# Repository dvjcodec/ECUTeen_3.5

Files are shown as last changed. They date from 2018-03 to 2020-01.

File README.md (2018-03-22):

# ECUTeen_3.5 rev.A (not tested!)

Stand Alone ECU with Teensy 3.5

On the board:
- 4 injection chanels
- 4 ignition chanels (for active coils)
- 2 high current PWM chanels
- IDLE out
- BOOST out
- stepper motor 
- 3x low current outs (FAN, FUEL, LC1)
- BlueTooth connector
- Clutch control
- tachometer out
- 5V power supply with LM2596
- 2x O2 sensor input
- CAN
- inlet air temperature sensor input
- coolant temperature sensor input
- throttle position sensor input
- 2x HALL input or VR
- MAP sensor 3bar

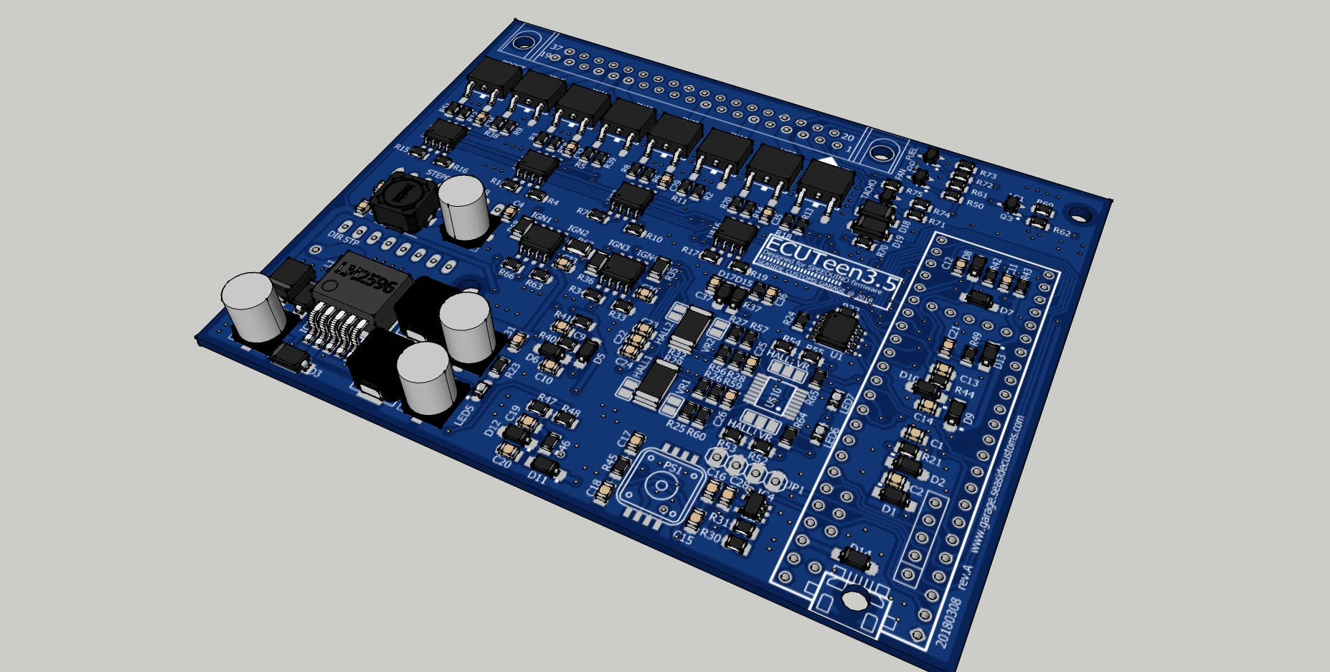
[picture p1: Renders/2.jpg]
Board


## Firmware

Designed for firmware
[Speeduino](https://speeduino.com/forum/viewtopic.php?f=13&t=1593)

## License

[CC BY-NC 3.0](https://creativecommons.org/licenses/by-nc/3.0/)

## Authors

Krzysztof Dymianiuk @ Seaside Customs Garage
http://www.garage.seasidecustoms.com

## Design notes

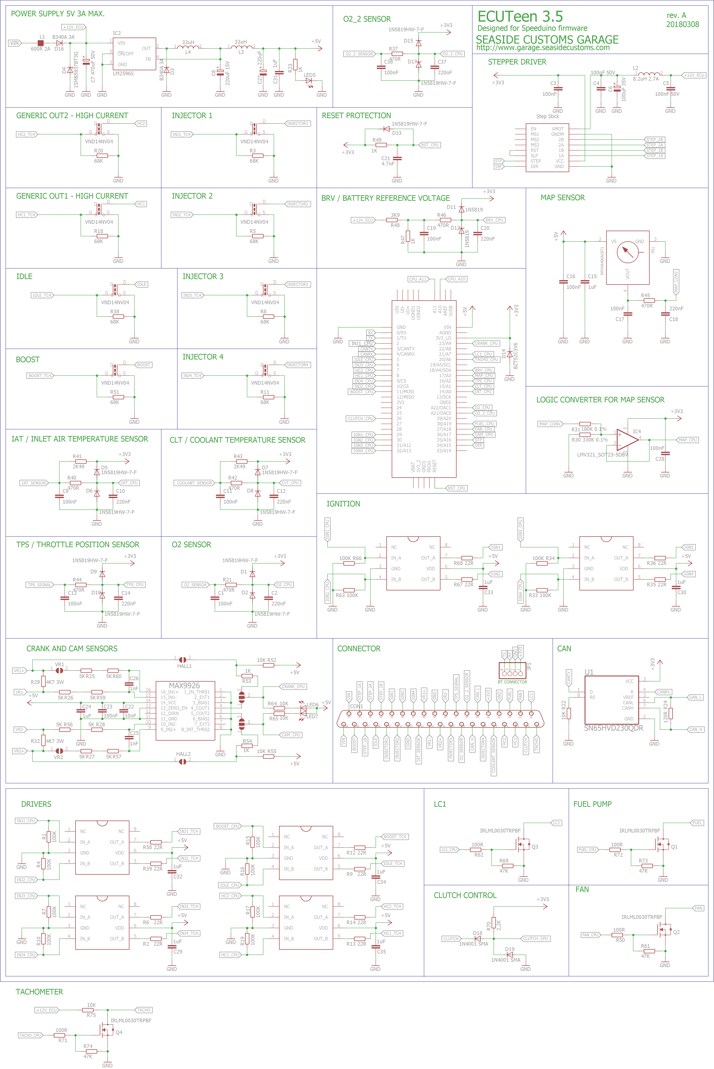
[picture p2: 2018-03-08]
schematic.png

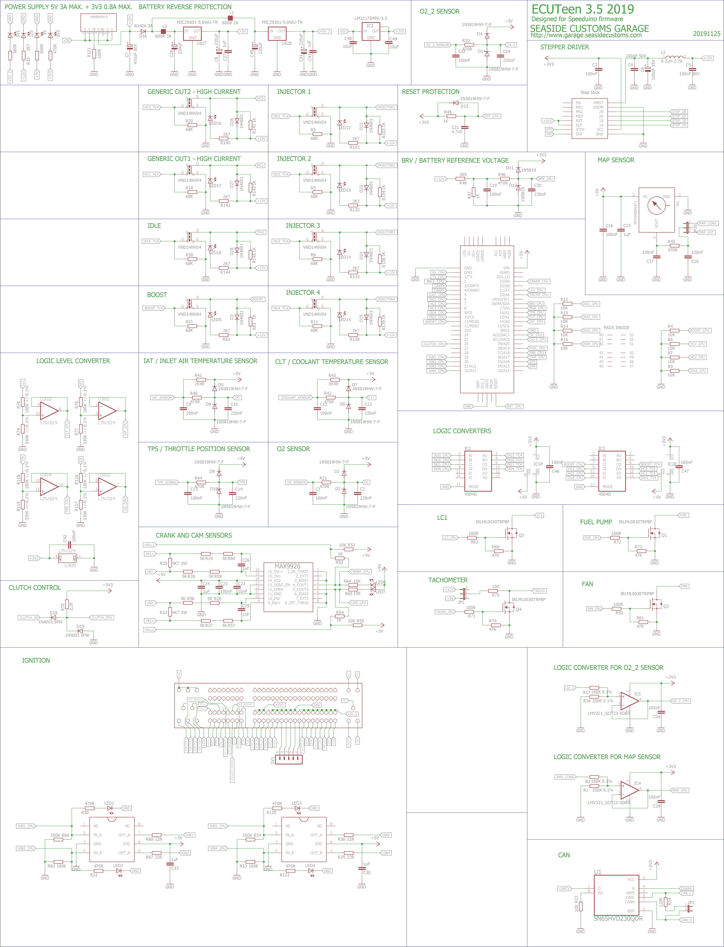
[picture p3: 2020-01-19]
ECUTeen3_5_2019_schematic.png

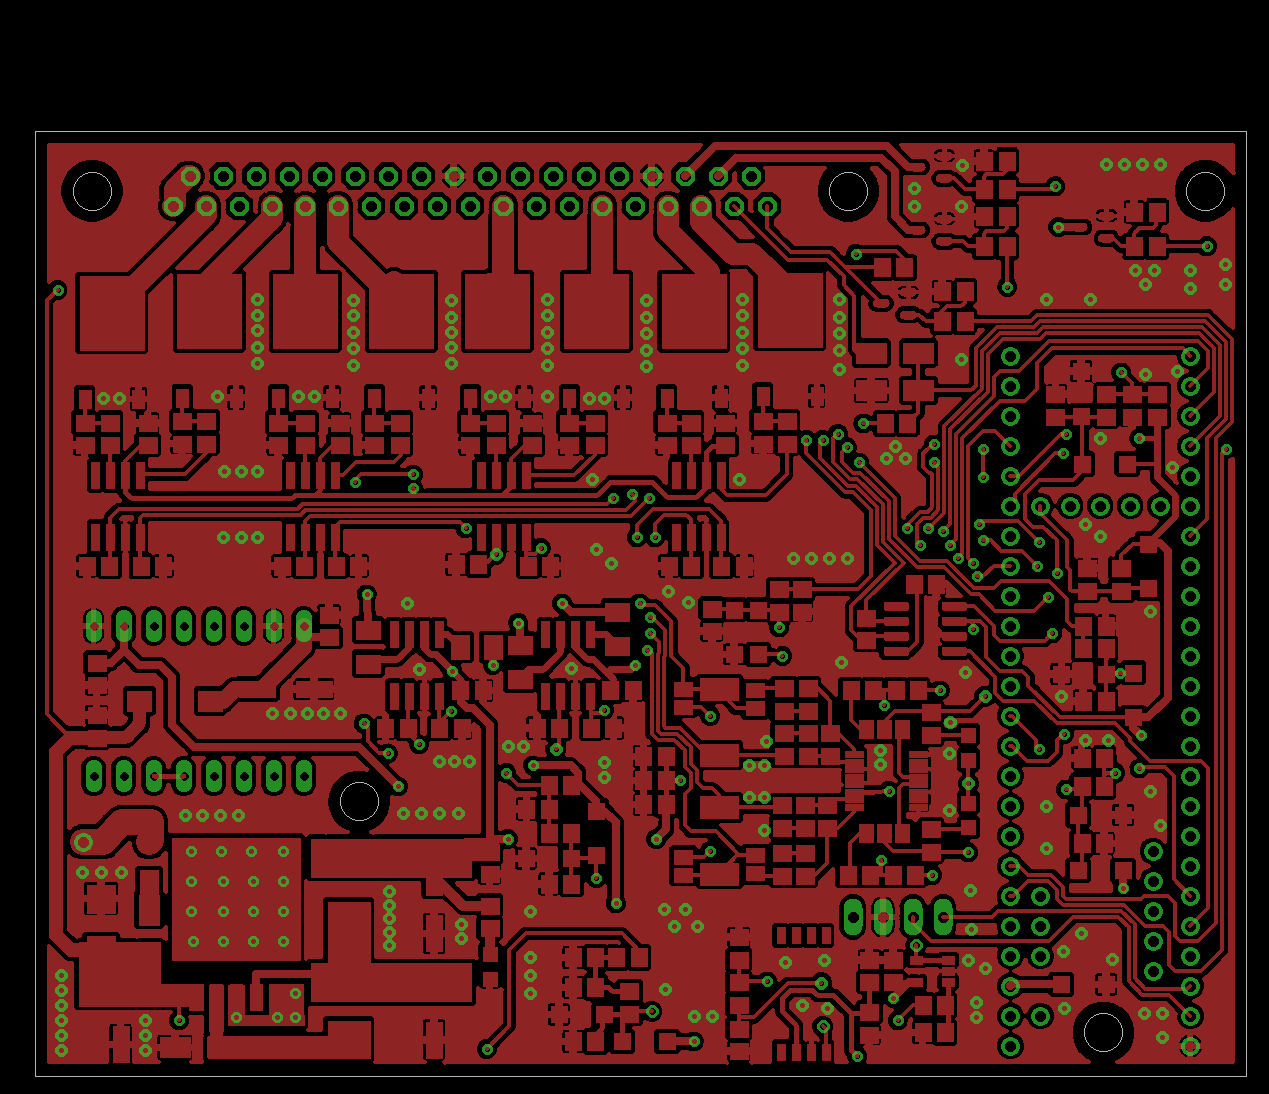
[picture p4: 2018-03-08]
Renders/TOP.png

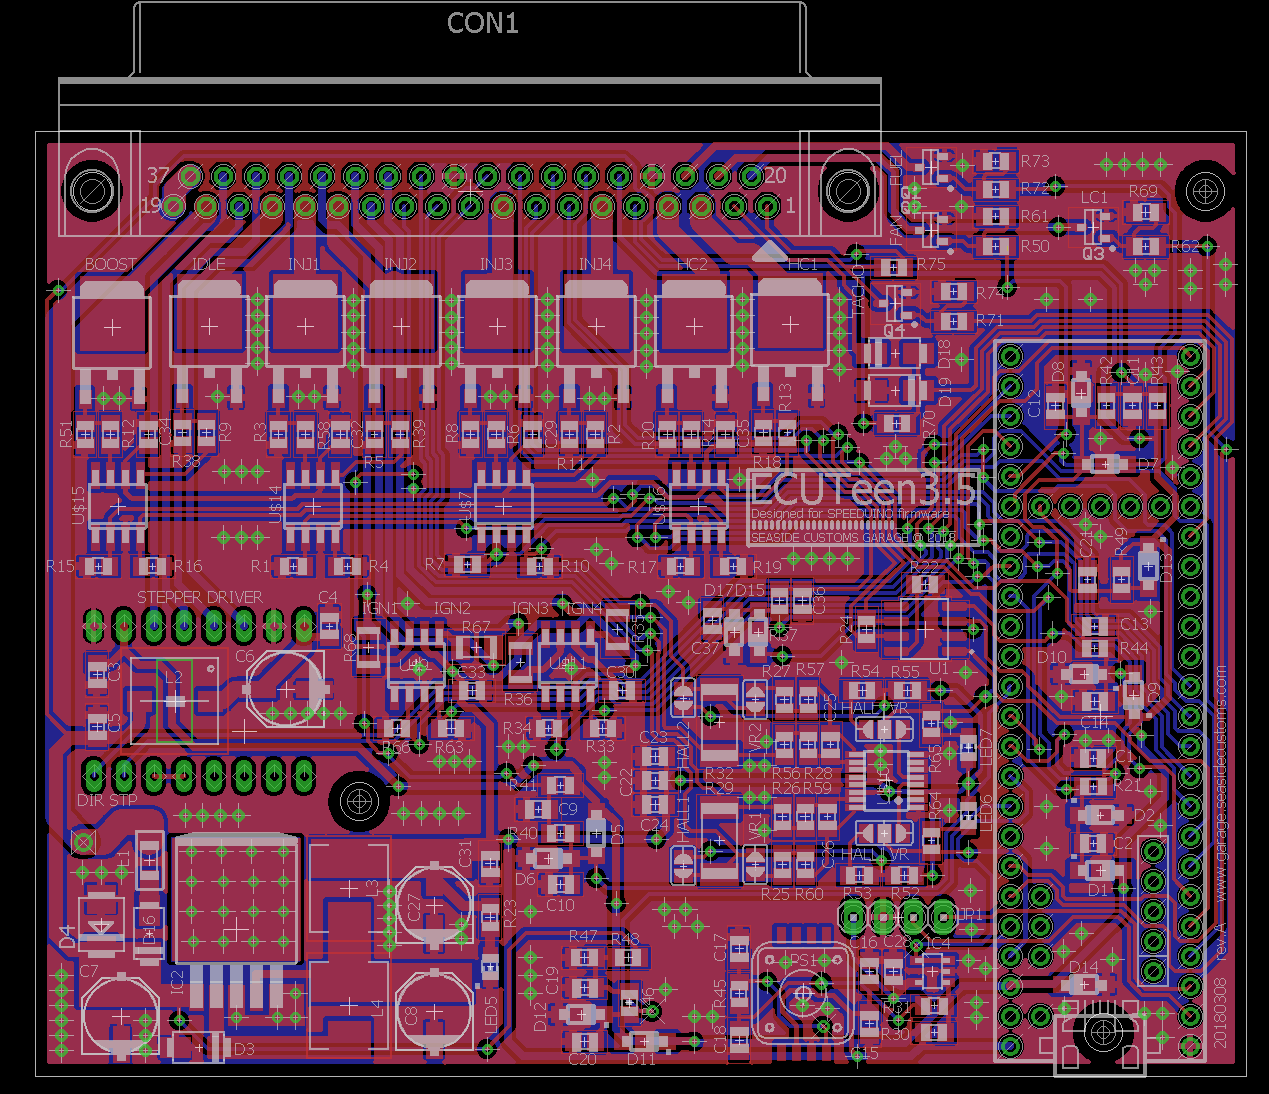
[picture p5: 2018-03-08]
Renders/ecuteen.png

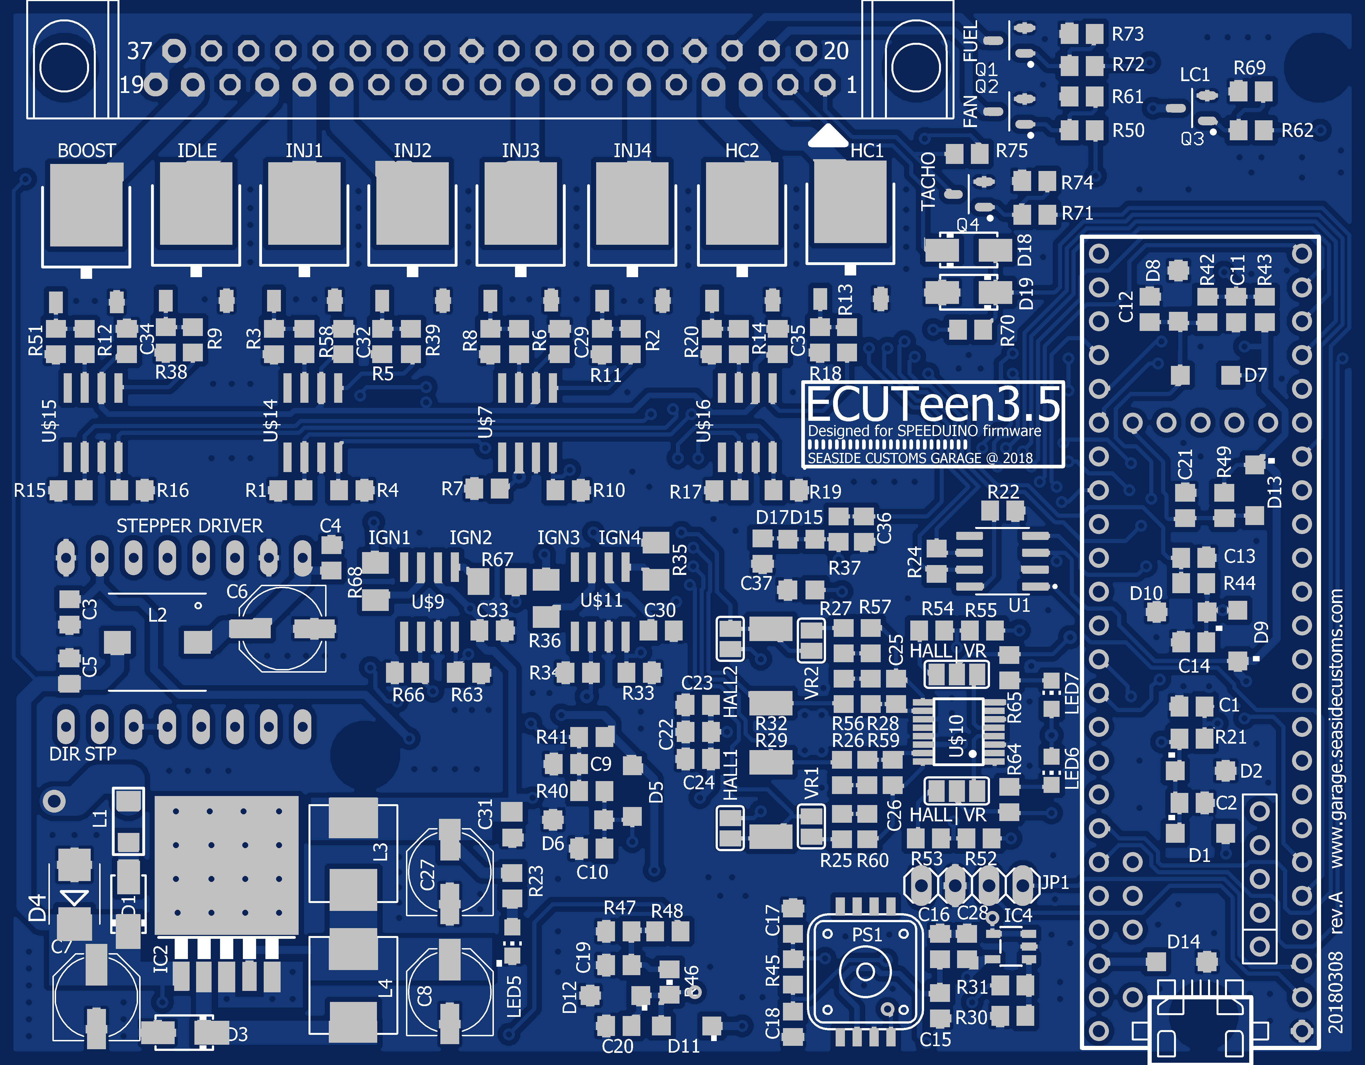
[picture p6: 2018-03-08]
Renders/eagleUp_ECUTeen3.5_rev.A_20180308_1928_board_top.png

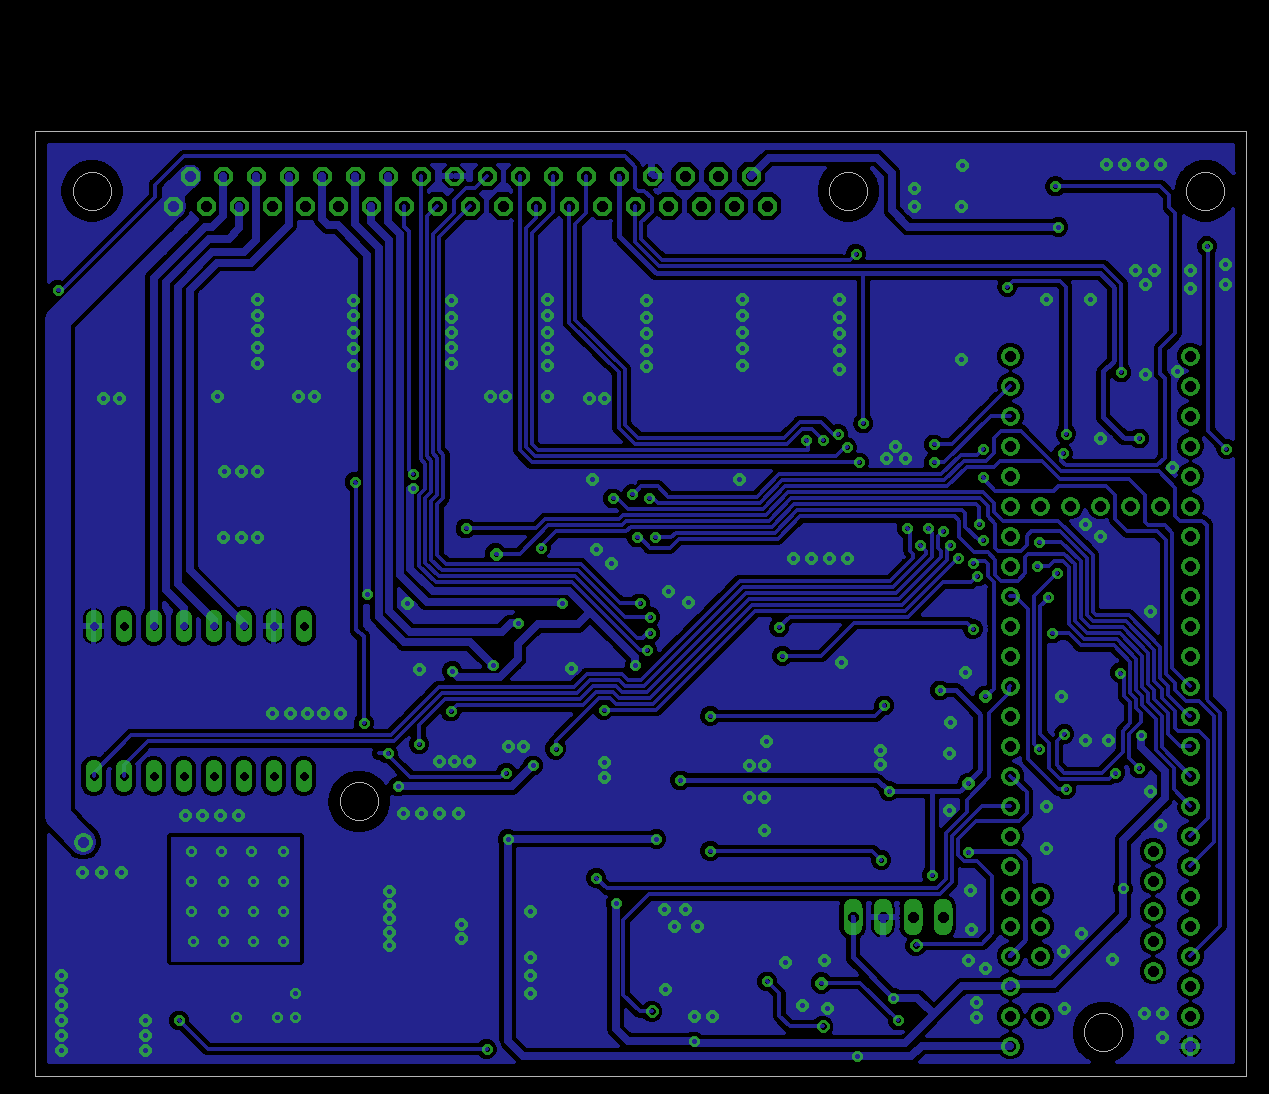
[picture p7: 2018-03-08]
Renders/BOTTOM.png

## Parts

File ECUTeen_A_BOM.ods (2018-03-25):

Element | Value | Package | Other | Link
C1, C3, C4, C5, C9, C11, C13, 16, C17, C19, C23, C28, C36, | 100nF | 0805 | C4,C5 – 50V, rest 35V
C2, C10, C12, C14, C18, C20, C37 | 220nF | 0805
C6 | 100uF/35V | CPOL, PANASONIC_D
C7 | 470uF/50V | CPOL, PANASONIC_D
C8, C27 | 220uF/35V | CPOL, PANASONIC_D
C15, C24, C29, C30, C31, C32, C33, C34, C35 | 1uF | 0805
C21 | 4.7nF | 0805
C22 | 10nF | 0805
C25, C26 | 1nF | 0805
CON1 | DB37 | male connector / angled
D1, D2, D5, D6, D7, D8, D9, D10, D13, D15, D17 | 1N5819HW-7-F | SOD123
D3, D16 | B340A 3A S1A | DO214AC
D4 | 1SMB5937BT3G | ZENER-DIODE SMB
D11, D12 | 1N5819 | SOD123
D14 | BZT52C3V6 | SOD123
D18, D19 | 1N4001 SMA S1A | DO214AC
IC2 | LM2596S | TO263-5 | Converter 150 kHz 3A Step-Down Voltage Regulator
IC4 | LMV321_SOT23-5DBV | SOT23-5
JP1 | PINHD-1X4 | Pin header 2.54
L1 | 600R 2A | L1206 | FERRITE BEAD Wurth 74279218
L2 | 8.2uH 2.7A | WE-PD_7332/7345_PLASTIC_BASE | WURTH 7447779008
L3, L4 | 33uH | WE-LHMI_7030/7050 | Wurth 74437349330
LED5, LED6, LED7 | LED DIODE | 0805
PS1 | MPXH6400AC6T1 | 1317A
Q1, Q2, Q3, Q4 | IRLML0030TRPBF | MOSFET-NCH_SOT-23
R1, R4, R7, R10, R15, R16, R17, R19, R33, R34, R63, R66 | 100K | 0805
R2, R6, R9, R12, R13, R14, R35, R36, R39, R58, R67, R68 | 22R | 0805
R3, R5, R8, R11, R18, R20, R38, R51 | 68K | 0805
R21, R37, R40, R42, R44, R45, R46 | 470R | 0805
R22, R52, R55, R64, R65, R75 | 10K | 0805
R23, R47, R49, R53, R54 | 1K | 0805
R24 | 120R | 0805
R25, R26, R27, R28, R56, R57, R59, R60 | 5K | 0805
R29, R32 | 4K7 3W | 2512
R30 | 330K 0.1% | 0805
R31 | 180K 0.1% | 0805
R41, R43 | 2K49 | 0805
R48 | 3K9 | 0805
R50, R62, R71, R72 | 100R | 0805
R61, R69, R73, R74 | 47K | 0805
R70 | 2K2 | 0805
U$1 | TEENSY_3.5
U$2, U$3, U$4, U$5, U$6, U$8, U$12, U$13 | VND14NV04 | DPAK
U$7, U$9, U$11, U$14, U$15, U$16 | TC427SO-8 | SO-8
U$10 | MAX9926 | QSOP16
U1 | SN65HVD230QDR | SOIC127P600X175-8N | Catalog 3.3-V CAN Transceivers

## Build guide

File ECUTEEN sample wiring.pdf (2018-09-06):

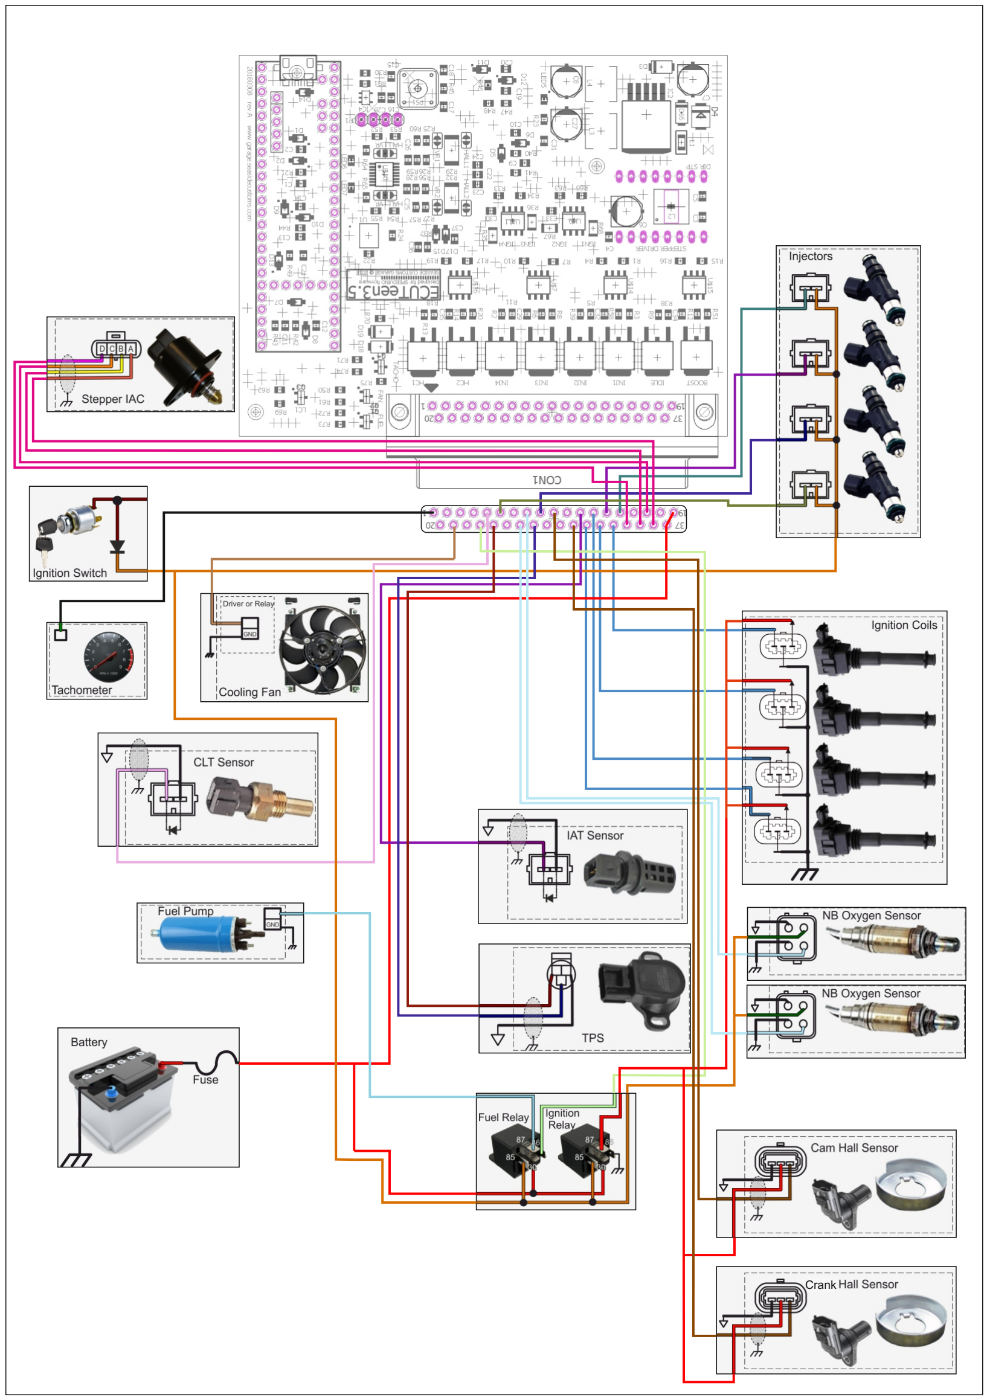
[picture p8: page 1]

Crank

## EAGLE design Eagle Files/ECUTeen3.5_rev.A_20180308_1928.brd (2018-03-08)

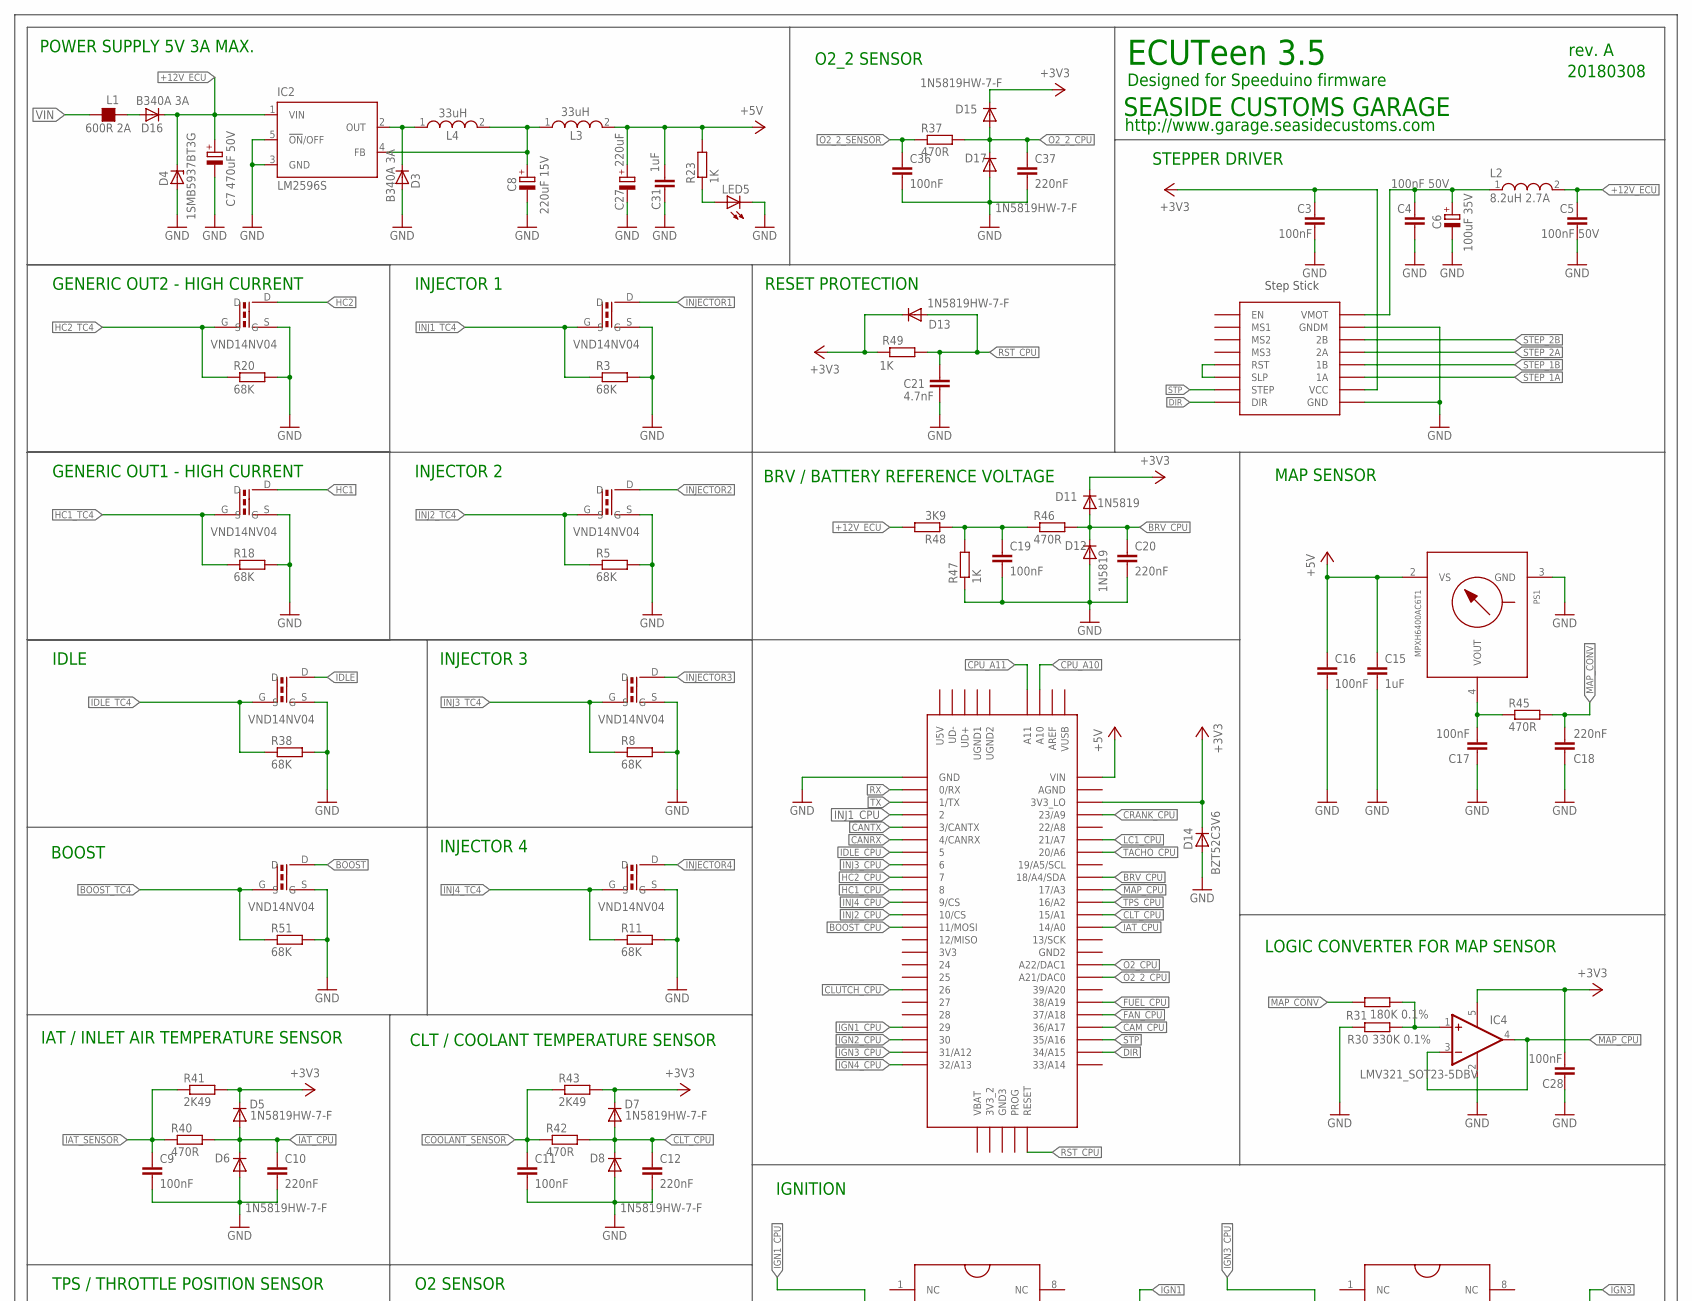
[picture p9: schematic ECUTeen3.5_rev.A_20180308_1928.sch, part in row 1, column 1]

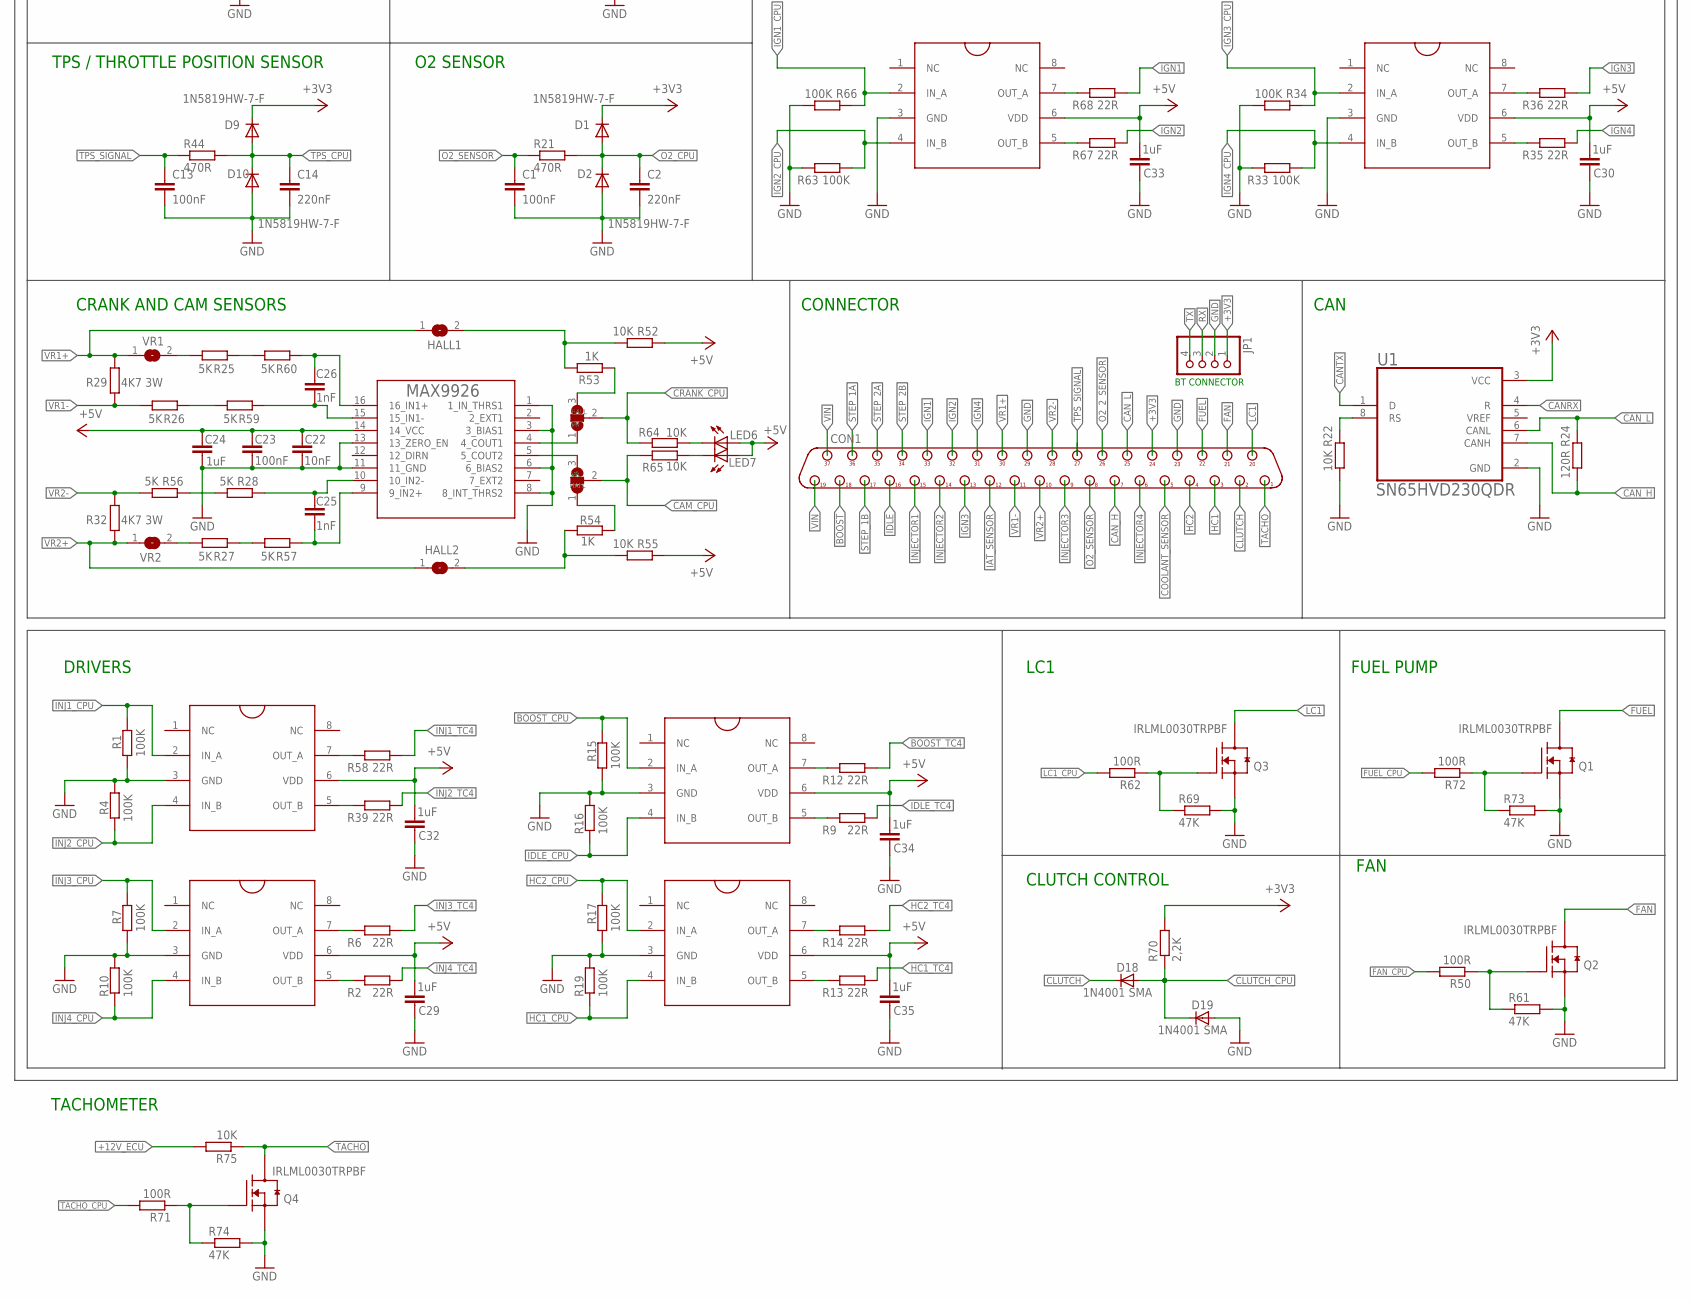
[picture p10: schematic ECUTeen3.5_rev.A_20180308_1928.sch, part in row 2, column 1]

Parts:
C1, C3, C9, C11, C13, C16, C17, C19, C23, C28, C36: 100nF; C0805
C2, C10, C12, C14, C18, C20, C37: 220nF; C0805
C4, C5: 100nF 50V; C0805
C6: 100uF 35V; PANASONIC_D
C7: 470uF 50V; PANASONIC_D
C8: 220uF 15V; PANASONIC_D
C15, C24, C29, C30, C31, C32, C33, C34, C35: 1uF; C0805
C21: 4.7nF; C0805
C22: 10nF; C0805
C25, C26: 1nF; C0805
C27: 220uF; PANASONIC_D
CON1: DB37M/90; D-37M/90
D1, D2, D5, D6, D7, D8, D9, D10, D13, D15, D17: 1N5819HW-7-F; SOD123
D3, D16: B340A 3A; DO214AC
D4: 1SMB5937BT3G; SMB
D11, D12: 1N5819; SOD123
D14: BZT52C3V6; SOD123
D18, D19: 1N4001 SMA; DO214AC
IC2: LM2596S; TO263-5
IC4: LMV321_SOT23-5DBV; SOT23-5
JMP1, JMP2: SJ2W; SJ_2
JP1: PINHD-1X4; 1X04
L1: 600R 2A; L1206
L2: 8.2uH 2.7A; WE-PD_7332/7345_PLASTIC_BASE
L3, L4: 33uH; WE-LHMI_7030/7050
LED5, LED6, LED7: LEDCHIP-LED0805; CHIP-LED0805
PS1: MPXH6400AC6T1; 1317A
Q1, Q2, Q3, Q4: IRLML0030TRPBF; SOT95P280X135-3N
R1, R4, R7, R10, R15, R16, R17, R19, R33, R34, R63, R66: 100K; R0805
R2, R6, R9, R12, R13, R14, R39, R58: 22R; R0805
R3, R5, R8, R11, R18, R20, R38, R51: 68K; R0805
R21, R37, R40, R42, R44, R45, R46: 470R; R0805
R22, R52, R55, R64, R65, R75: 10K; R0805
R23, R47, R49, R53, R54: 1K; R0805
R24: 120R; R0805
R25, R26, R27, R28, R56, R57, R59, R60: 5K; R0805
R29, R32: 4K7 3W; R2512
R30: 330K 0.1%; R0805
R31: 180K 0.1%; R0805
R35, R36, R67, R68: 22R; M1206
R41, R43: 2K49; R0805
R48: 3K9; R0805
R50, R62, R71, R72: 100R; R0805
R61, R69, R73, R74: 47K; R0805
R70: 2,2K; R0805
SJ3: VR2; SJ
SJ4: VR1; SJ
SJ5: HALL2; SJ
SJ6: HALL1; SJ
STEPSTICK-X: STEP-STICK
U1: SN65HVD230QDR; SOIC127P600X175-8N
U$1: TEENSY_3.5/3.6
U$2, U$3, U$4, U$5, U$6, U$8, U$12, U$13: DPAK_N-CHANNEL_MOSFET
U$7, U$9, U$11, U$14, U$15, U$16: TC427SO-8; SO-8
U$10: MAX9926; QSOP16

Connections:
+3V3: C3.1, C28.2, CON1.24, D1.C, D5.C, D7.C, D9.C, D11.C, D13.C, D14.C, D15.C, IC4.5 (V+), JP1.1, R41.2, R43.2, R49.1, R70.2, STEPSTICK-X.VCC, U1.3 (VCC), U$1.3V3_LO
+5V: C15.1, C16.1, C22.1, C23.1, C24.1, C27.+, C29.2, C30.2, C31.1, C32.2, C33.2, C34.2, C35.2, L3.2, LED6.A, LED7.A, PS1.2 (VS), R23.2, R52.1, R55.1, U$1.VIN, U$7.6 (VDD), U$9.6 (VDD), U$10.14 (14_VCC), U$11.6 (VDD), U$14.6 (VDD), U$15.6 (VDD), U$16.6 (VDD)
+12V_ECU: C5.1, C7.+, D4.C, D16.C, IC2.1 (VIN), L2.2, R48.2, R75.2
BOOST: CON1.18, U$13.D
BOOST_CPU: R15.2, U$1.11/MOSI, U$15.2 (IN_A)
BOOST_TC4: R12.2, R51.1, U$13.G
BRV_CPU: C20.1, D11.A, D12.C, R46.2, U$1.18/A4/SDA
CAM_CPU: JMP2.2, R65.1, U$1.36/A17
CANRX: U1.4 (R), U$1.4/CANRX
CANTX: U1.1 (D), U$1.3/CANTX
CAN_H: CON1.7, R24.2, U1.7 (CANH)
CAN_L: CON1.25, R24.1, U1.6 (CANL)
CLT_CPU: C12.1, D7.A, D8.C, R42.2, U$1.15/A1
CLUTCH: CON1.2, D18.C
CLUTCH_CPU: D18.A, D19.C, R70.1, U$1.26
COOLANT_SENSOR: C11.1, CON1.5, R42.1, R43.1
CPU_A10: U$1.A10
CPU_A11: U$1.A11
CRANK_CPU: JMP1.2, R64.1, U$1.23/A9
DIR: STEPSTICK-X.DIR, U$1.34/A15
FAN: CON1.21, Q2.3 (D)
FAN_CPU: R50.2, U$1.37/A18
FUEL: CON1.22, Q1.3 (D)
FUEL_CPU: R72.2, U$1.38/A19
GND: C1.2, C2.2, C3.2, C4.2, C5.2, C6.-, C7.-, C8.-, C9.2, C10.2, C11.2, C12.2, C13.2, C14.2, C15.2, C16.2, C17.1, C18.1, C19.2, C20.2, C21.2, C22.2, C23.2, C24.2, C27.-, C28.1, C29.1, C30.1, C31.2, C32.1, C33.1, C34.1, C35.1, C36.2, C37.2, CON1.23, CON1.29, D2.A, D3.A, D4.A, D6.A, D8.A, D10.A, D12.A, D14.A, D17.A, D19.A, IC2.3 (GND), IC2.5 (!ON!/OFF), IC4.2 (V-), JP1.2, LED5.C, PS1.3 (GND), Q1.2 (S), Q2.2 (S), Q3.2 (S), Q4.2 (S), R1.1, R3.2, R4.1, R5.2, R7.1, R8.2, R10.1, R11.2, R15.1, R16.1, R17.1, R18.2, R19.1, R20.2, R22.2, R30.1, R33.1, R34.2, R38.2, R47.1, R51.2, R61.2, R63.1, R66.2, R69.2, R73.2, R74.2, STEPSTICK-X.GND, STEPSTICK-X.GNDM, U1.2 (GND), U$1.GND, U$2.S, U$3.S, U$4.S, U$5.S, U$6.S, U$7.3 (GND), U$8.S, U$9.3 (GND), U$10.1 (1_IN_THRS1), U$10.3 (3_BIAS1), U$10.6 (6_BIAS2), U$10.8 (8_INT_THRS2), U$10.11 (11_GND), U$10.13 (13_ZERO_EN), U$11.3 (GND), U$12.S, U$13.S, U$14.3 (GND), U$15.3 (GND), U$16.3 (GND)
HC1: CON1.3, U$3.D
HC1_CPU: R19.2, U$1.8, U$16.4 (IN_B)
HC1_TC4: R13.2, R18.1, U$3.G
HC2: CON1.4, U$2.D
HC2_CPU: R17.2, U$1.7, U$16.2 (IN_A)
HC2_TC4: R14.2, R20.1, U$2.G
IAT_CPU: C10.1, D5.A, D6.C, R40.2, U$1.14/A0
IAT_SENSOR: C9.1, CON1.12, R40.1, R41.1
IDLE: CON1.16, U$5.D
IDLE_CPU: R16.2, U$1.5, U$15.4 (IN_B)
IDLE_TC4: R9.2, R38.1, U$5.G
IGN1: CON1.33, R68.2
IGN1_CPU: R66.1, U$1.29, U$9.2 (IN_A)
IGN2: CON1.32, R67.2
IGN2_CPU: R63.2, U$1.30, U$9.4 (IN_B)
IGN3: CON1.13, R36.2
IGN3_CPU: R34.1, U$1.31/A12, U$11.2 (IN_A)
IGN4: CON1.31, R35.2
IGN4_CPU: R33.2, U$1.32/A13, U$11.4 (IN_B)
INJ1_CPU: R1.2, U$1.2, U$14.2 (IN_A)
INJ1_TC4: R3.1, R58.2, U$12.G
INJ2_CPU: R4.2, U$1.10/CS, U$14.4 (IN_B)
INJ2_TC4: R5.1, R39.2, U$4.G
INJ3_CPU: R7.2, U$1.6, U$7.2 (IN_A)
INJ3_TC4: R6.2, R8.1, U$6.G
INJ4_CPU: R10.2, U$1.9/CS, U$7.4 (IN_B)
INJ4_TC4: R2.2, R11.1, U$8.G
INJECTOR1: CON1.15, U$12.D
INJECTOR2: CON1.14, U$4.D
INJECTOR3: CON1.9, U$6.D
INJECTOR4: CON1.6, U$8.D
LC1: CON1.20, Q3.3 (D)
LC1_CPU: R62.2, U$1.21/A7
MAP_CONV: C18.2, R31.2, R45.2
MAP_CPU: IC4.3 (-IN), IC4.4 (OUT), U$1.17/A3
unnamed: JMP1.1, U$10.4 (4_COUT1)
unnamed: JMP1.3, R53.2
unnamed: R67.1, U$9.5 (OUT_B)
unnamed: JMP2.3, U$10.5 (5_COUT2)
unnamed: R68.1, U$9.7 (OUT_A)
unnamed: R35.1, U$11.5 (OUT_B)
unnamed: JMP2.1, R54.1
unnamed: R36.1, U$11.7 (OUT_A)
unnamed: Q2.1 (G), R50.1, R61.1
unnamed: R2.1, U$7.5 (OUT_B)
unnamed: Q3.1 (G), R62.1, R69.1
unnamed: R22.1, U1.8 (RS)
unnamed: STEPSTICK-X.RST, STEPSTICK-X.SLP
unnamed: C4.1, C6.+, L2.1, STEPSTICK-X.VMOT
unnamed: IC4.1 (+IN), R30.2, R31.1
unnamed: C19.1, R46.1, R47.2, R48.1
unnamed: R54.2, R55.2, SJ5.2
unnamed: Q4.1 (G), R71.1, R74.1
unnamed: C17.2, PS1.4 (VOUT), R45.1
unnamed: R52.2, R53.1, SJ6.2
unnamed: C25.2, R57.1, U$10.9 (9_IN2+)
unnamed: C26.1, R60.1, U$10.16 (16_IN1+)
unnamed: C26.2, R59.1, U$10.15 (15_IN1-)
unnamed: C25.1, R28.1, U$10.10 (10_IN2-)
unnamed: R25.1, R60.2
unnamed: R27.2, SJ3.2
unnamed: R25.2, SJ4.2
unnamed: LED7.C, R65.2
unnamed: LED6.C, R64.2
unnamed: D16.A, L1.1
unnamed: R6.1, U$7.7 (OUT_A)
unnamed: R9.1, U$15.5 (OUT_B)
unnamed: LED5.A, R23.1
unnamed: R26.1, R59.2
unnamed: R27.1, R57.2
unnamed: R28.2, R56.1
unnamed: R12.1, U$15.7 (OUT_A)
unnamed: R13.1, U$16.5 (OUT_B)
unnamed: R39.1, U$14.5 (OUT_B)
unnamed: R14.1, U$16.7 (OUT_A)
unnamed: R58.1, U$14.7 (OUT_A)
unnamed: Q1.1 (G), R72.1, R73.1
unnamed: D3.C, IC2.2 (OUT), L4.1
O2_2_CPU: C37.1, D15.A, D17.C, R37.2, U$1.21/DAC0 (A21/DAC0)
O2_2_SENSOR: C36.1, CON1.26, R37.1
O2_CPU: C2.1, D1.A, D2.C, R21.2, U$1.A22/DAC1
O2_SENSOR: C1.1, CON1.8, R21.1
RST_CPU: C21.1, D13.A, R49.2, U$1.RESET
RX: JP1.3, U$1.0/RX
STEP_1A: CON1.36, STEPSTICK-X.1A
STEP_1B: CON1.17, STEPSTICK-X.1B
STEP_2A: CON1.35, STEPSTICK-X.2A
STEP_2B: CON1.34, STEPSTICK-X.2B
STP: STEPSTICK-X.SPT (STEP), U$1.35/A16
SUPP1: C8.+, IC2.4 (FB), L3.1, L4.2
TACHO: CON1.1, Q4.3 (D), R75.1
TACHO_CPU: R71.2, U$1.20/A6
TPS_CPU: C14.1, D9.A, D10.C, R44.2, U$1.16/A2
TPS_SIGNAL: C13.1, CON1.27, R44.1
TX: JP1.4, U$1.1/TX
VIN: CON1.19, CON1.37, L1.2
VR1+: CON1.30, R29.1, SJ4.1, SJ6.1
VR1-: CON1.11, R26.2, R29.2
VR2+: CON1.10, R32.2, SJ3.1, SJ5.1
VR2-: CON1.28, R32.1, R56.2

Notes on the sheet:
INJECTOR 1
INJECTOR 2
INJECTOR 3
INJECTOR 4
BOOST
IDLE
GENERIC OUT1 - HIGH CURRENT
GENERIC OUT2 - HIGH CURRENT
O2 SENSOR
POWER SUPPLY 5V 3A MAX.
STEPPER DRIVER
ECUTeen 3.5
Designed for Speeduino firmware
rev. A
20180308
SEASIDE CUSTOMS GARAGE
http://www.garage.seasidecustoms.com
IAT / INLET AIR TEMPERATURE SENSOR
CLT / COOLANT TEMPERATURE SENSOR
TPS / THROTTLE POSITION SENSOR
MAP SENSOR
LOGIC CONVERTER FOR MAP SENSOR
BRV / BATTERY REFERENCE VOLTAGE
RESET PROTECTION
CRANK AND CAM SENSORS
CONNECTOR
IGNITION
HALL
DRIVERS
CAN
O2_2 SENSOR
BT CONNECTOR
FUEL PUMP
FAN
LC1
CLUTCH CONTROL
TACHOMETER

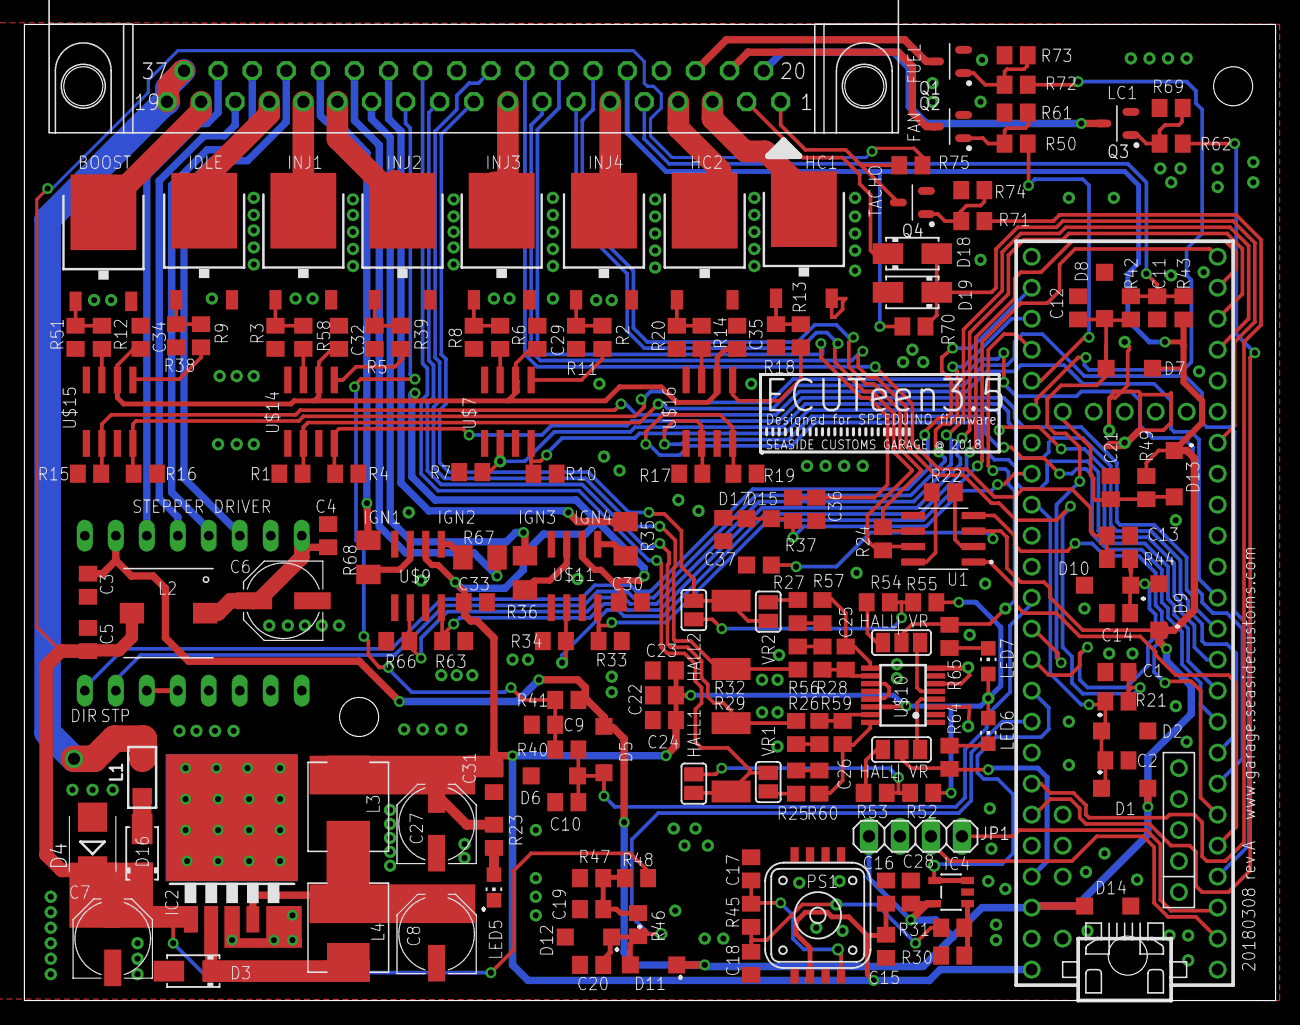
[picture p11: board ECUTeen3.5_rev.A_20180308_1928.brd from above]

Board: 2 copper layers, 102.5 x 80.0 mm, 171 parts (0 on the bottom side), 123 nets.

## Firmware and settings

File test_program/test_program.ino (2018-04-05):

// Simple "blinking LED's" program to test outputs 
// Krzysztof Dymianiuk @ Seaside Customs Garage

int led = 29;   //Ignition1
int led2 = 30;  //Ignition2
int led3 = 31;  //Ignition3
int led4 = 32;  //Ignition4
int led5 = 13;  //LED on Teensy
int led6 = 2;   //injector1
int led7 = 10;  //injector2
int led8 = 6;   //injector3
int led9 = 9;   //injector4
int led10 = 8;   //HC1
int led11 = 7;   //HC2
int led12 = 11;  //Boost
int led13 = 5;   //Idle
int led14 = 21;  //LC1
int led15 = 38;  //Fuel pump
int led16 = 37;  //Fan control
int led17 = 20;  //Tacho out


void setup() {               
// initialize the digital pin as an output.
pinMode(led, OUTPUT);
pinMode(led2, OUTPUT);
pinMode(led3, OUTPUT); 
pinMode(led4, OUTPUT);
pinMode(led5, OUTPUT);
pinMode(led6, OUTPUT);
pinMode(led7, OUTPUT);
pinMode(led8, OUTPUT);
pinMode(led9, OUTPUT);
pinMode(led10, OUTPUT);
pinMode(led11, OUTPUT);
pinMode(led12, OUTPUT);
pinMode(led13, OUTPUT);
pinMode(led14, OUTPUT);
pinMode(led15, OUTPUT);
pinMode(led16, OUTPUT);
pinMode(led17, OUTPUT);
}

void loop() 
{digitalWrite(led, HIGH);   // turn the LED on (HIGH is the voltage level)
delay(100);                 // wait for a second
digitalWrite(led, LOW);     // turn the LED off by making the voltage LOW
delay(100);                 // wait for a second

{digitalWrite(led2, HIGH);
delay(100);
digitalWrite(led2, LOW);
delay(100);}

{digitalWrite(led3, HIGH);
delay(100);
digitalWrite(led3, LOW);
delay(100);}

{digitalWrite(led4, HIGH);
delay(100);
digitalWrite(led4, LOW);
delay(100);}

{digitalWrite(led5, HIGH);
delay(100);
digitalWrite(led5, LOW);
delay(100);}

{digitalWrite(led6, HIGH);
delay(100);
digitalWrite(led6, LOW);
delay(100);}

{digitalWrite(led7, HIGH);
delay(100);
digitalWrite(led7, LOW);
delay(100);}

{digitalWrite(led8, HIGH);
delay(100);
digitalWrite(led8, LOW);
delay(100);}

{digitalWrite(led9, HIGH);
delay(100);
digitalWrite(led9, LOW);
delay(100);}

{digitalWrite(led10, HIGH);
delay(100);
digitalWrite(led10, LOW);
delay(100);}

{digitalWrite(led11, HIGH);
delay(100);
digitalWrite(led11, LOW);
delay(100);}

{digitalWrite(led12, HIGH);
delay(100);
digitalWrite(led12, LOW);
delay(100);}

{digitalWrite(led13, HIGH);
delay(100);
digitalWrite(led13, LOW);
delay(100);}

{digitalWrite(led14, HIGH);
delay(100);
digitalWrite(led14, LOW);
delay(100);}

{digitalWrite(led15, HIGH);
delay(100);
digitalWrite(led15, LOW);
delay(100);}

{digitalWrite(led16, HIGH);
delay(100);
digitalWrite(led16, LOW);
delay(100);}

{digitalWrite(led17, HIGH);
delay(100);
digitalWrite(led17, LOW);
delay(100);}

}

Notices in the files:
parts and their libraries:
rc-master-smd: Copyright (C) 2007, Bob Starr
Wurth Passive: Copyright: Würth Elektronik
